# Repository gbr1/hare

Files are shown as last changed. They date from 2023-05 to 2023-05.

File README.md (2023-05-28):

# hare

An open source and open hardware implementation for 4-wheeled mobile robots.

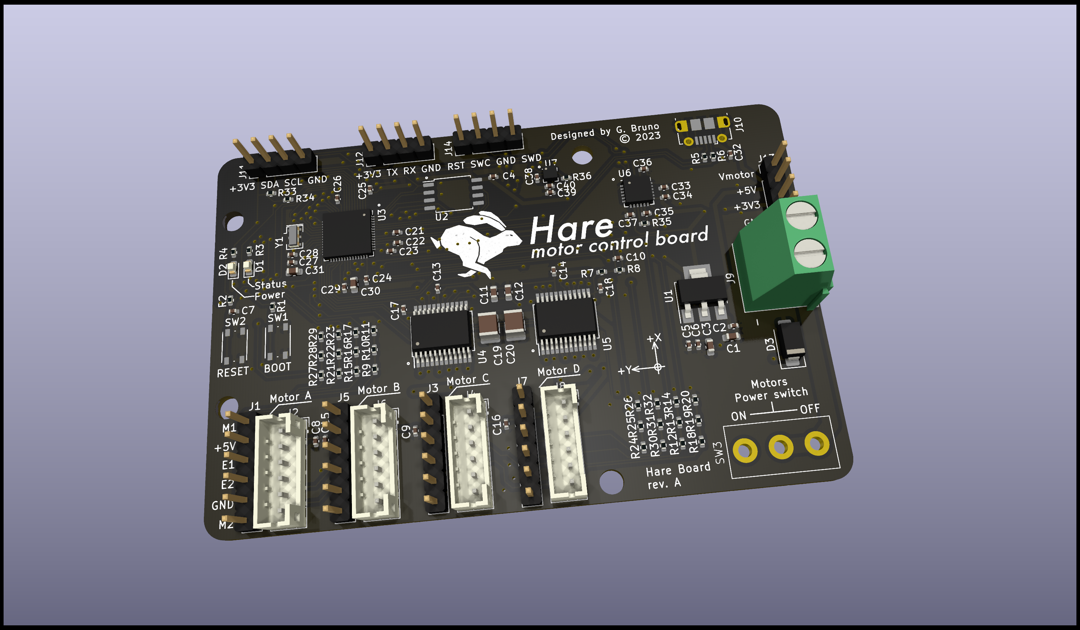
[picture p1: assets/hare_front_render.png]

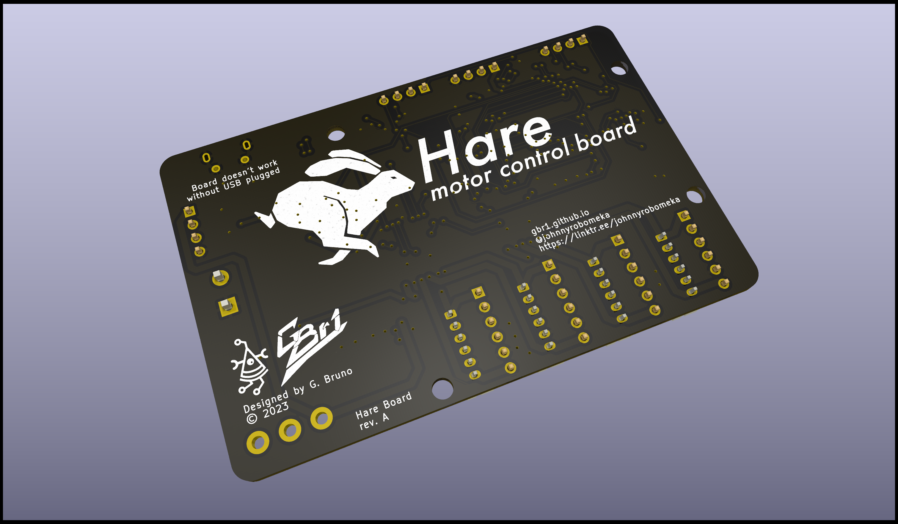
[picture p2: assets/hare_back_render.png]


It is compatible with ROS2 and DC brushed motors with encoder.

## Tech specs

- RP2040 MCU

- dual TB6612FNG motor drivers

- MPU6050 6DoF IMU

- LIS3MDL 3 axis magnetometer

- Power switch only for motors power supply

- 10-15V power input

- external connectors for I2C, debugger and UART

- compatibility with common motors with encoder (e.g. [moebiustech gearmotor](https://it.aliexpress.com/item/4000149449495.html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))

## License

The board is under **CC-4.0-BY-SA-NC** but ***dual licensing is available.***

<br>

For more info contact me.

## Links

- [firmware](https://github.com/gbr1/hare-arduino)

- [website](https://gbr1.github.io)

- [pizzarobotics](https://pizzarobotics.org)

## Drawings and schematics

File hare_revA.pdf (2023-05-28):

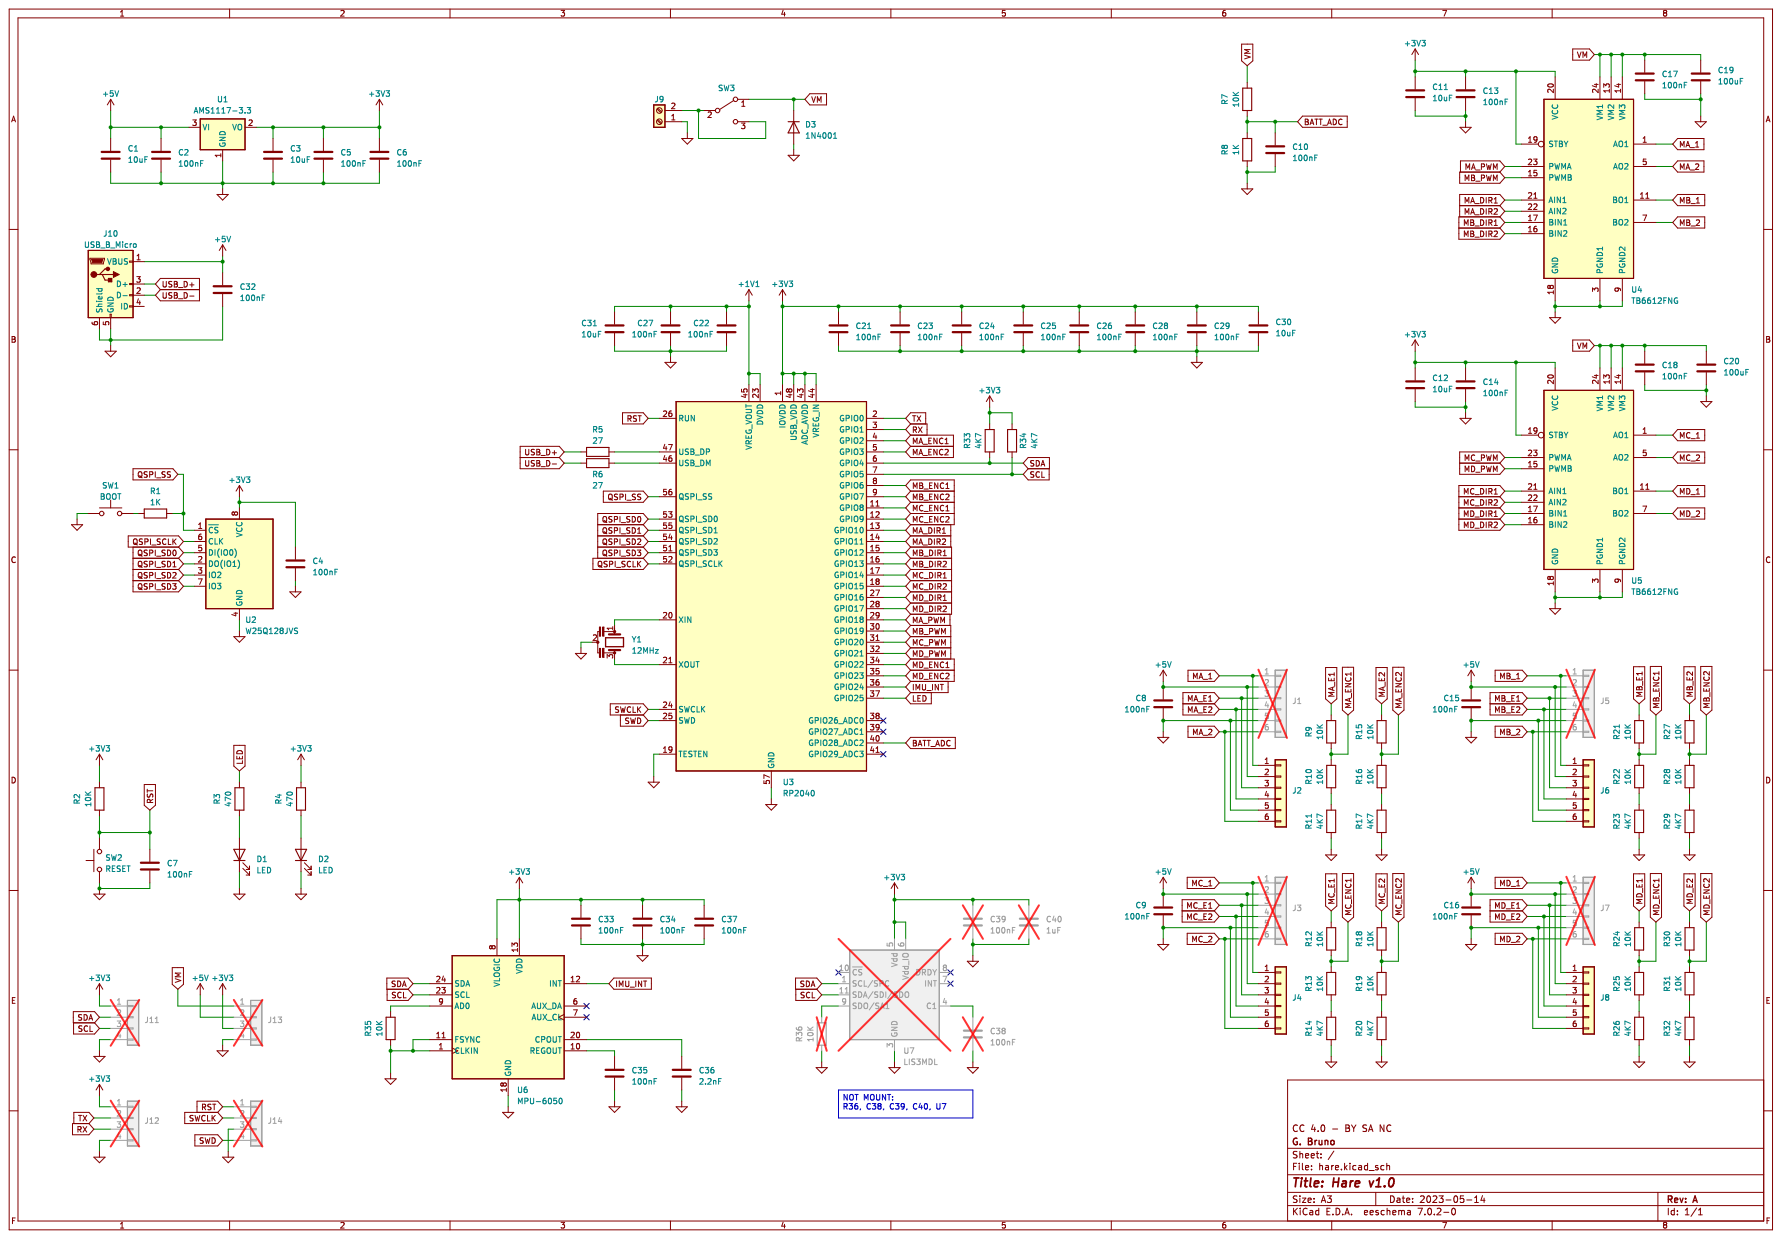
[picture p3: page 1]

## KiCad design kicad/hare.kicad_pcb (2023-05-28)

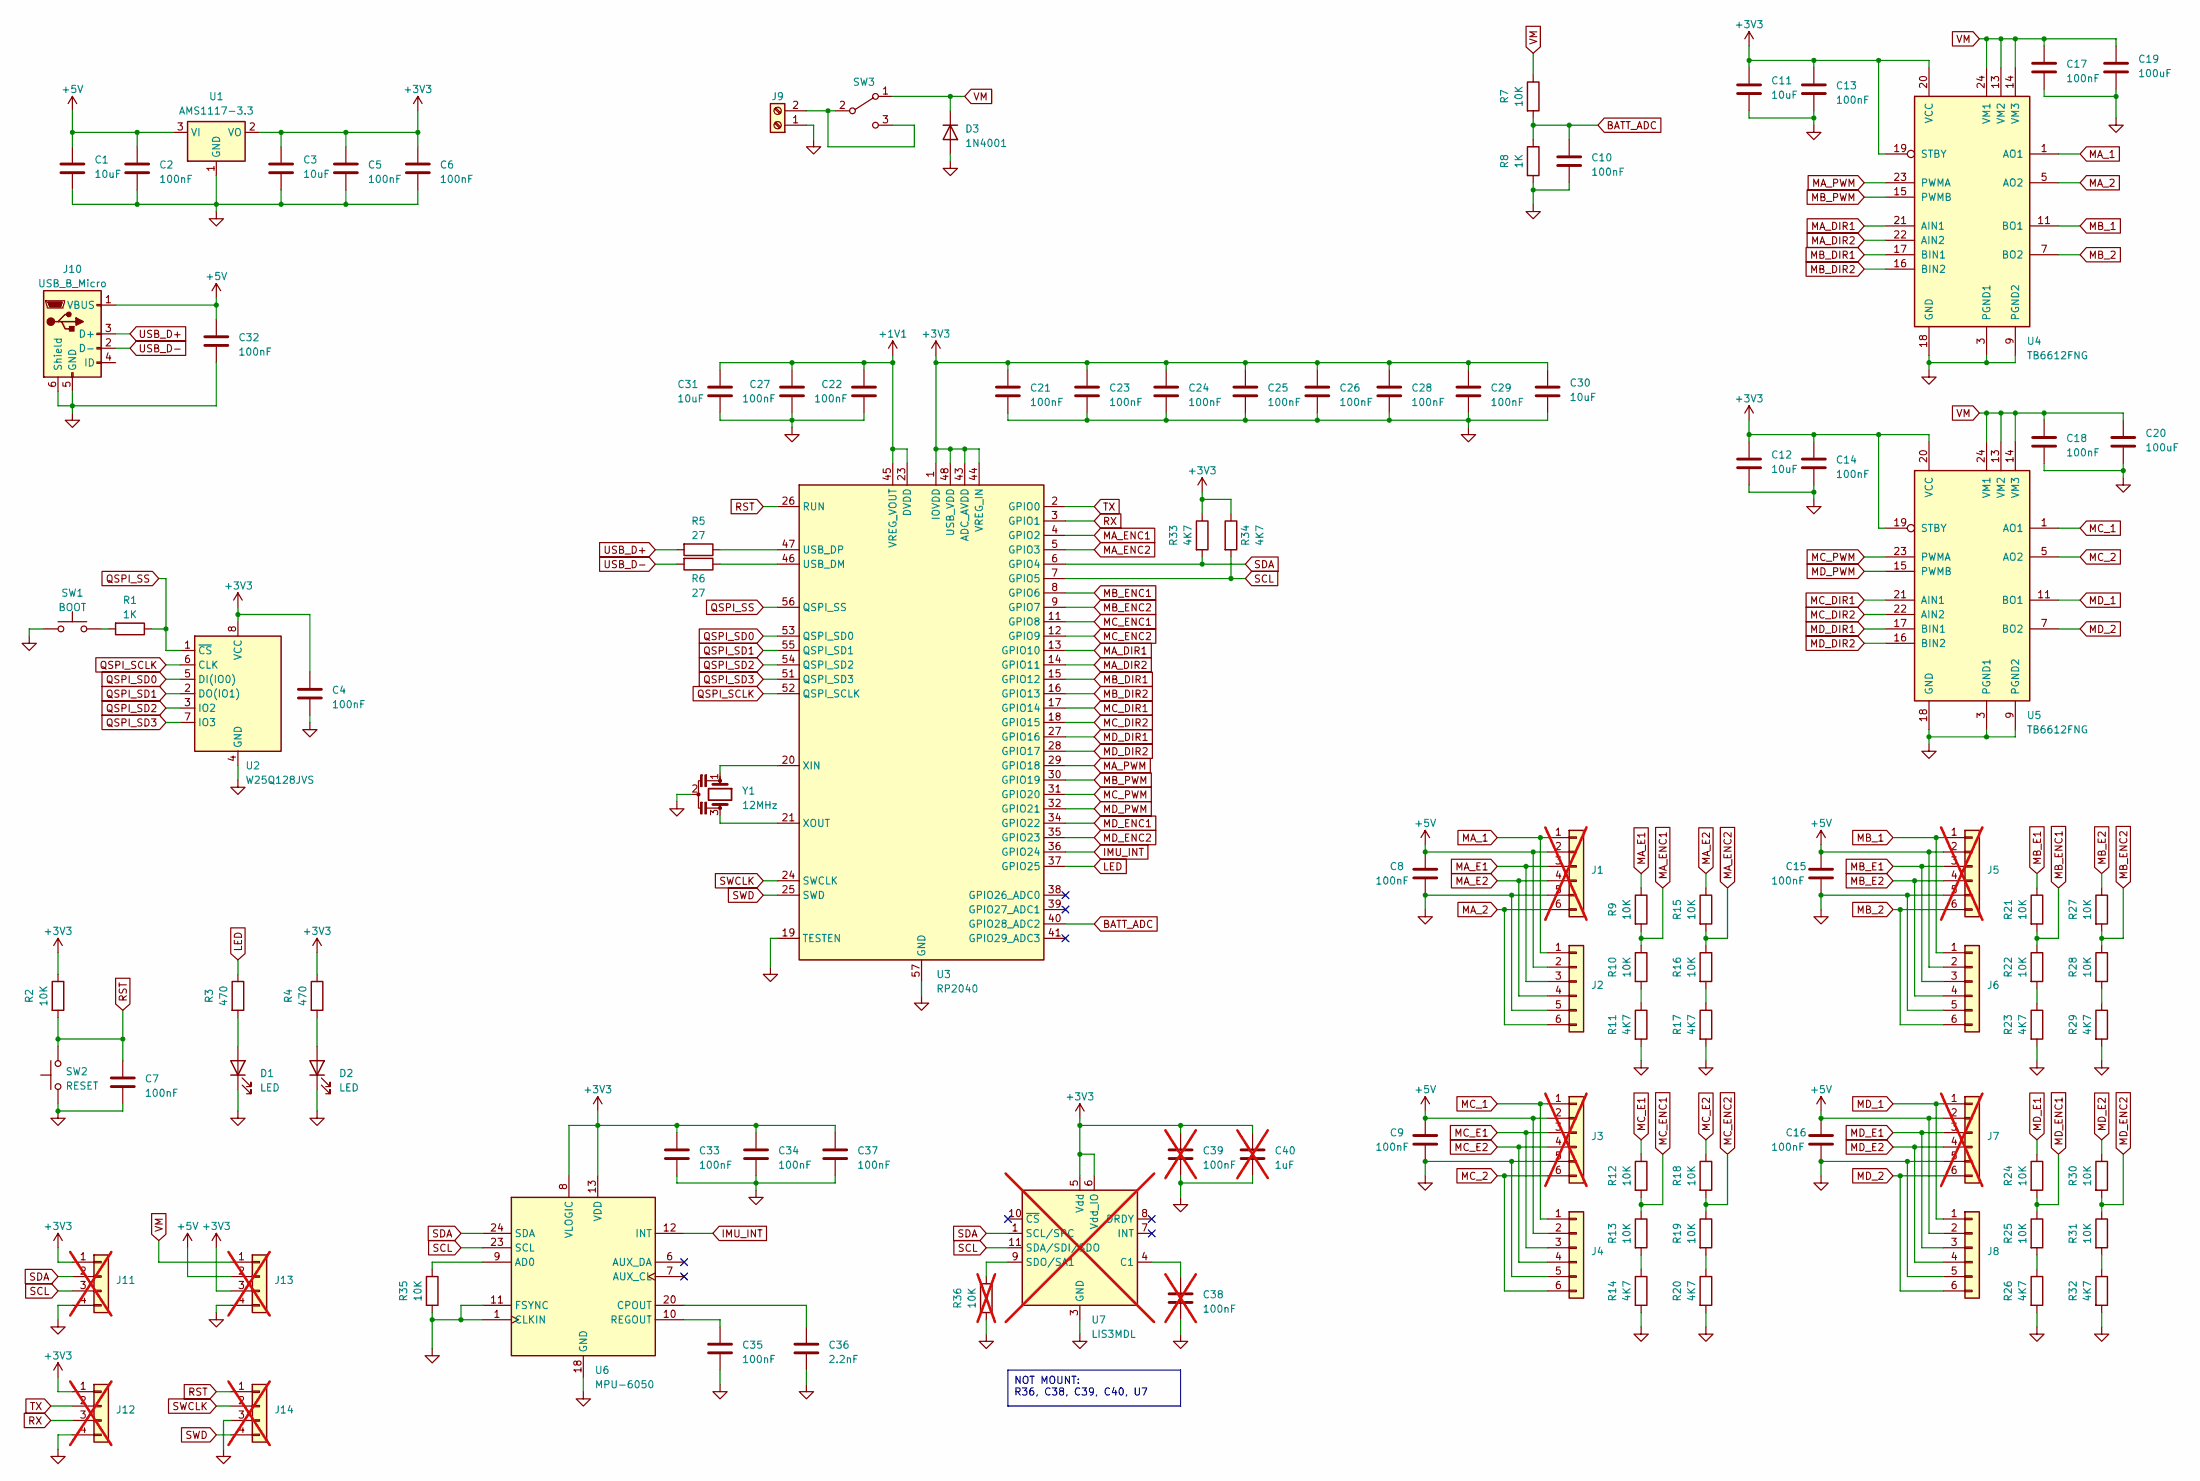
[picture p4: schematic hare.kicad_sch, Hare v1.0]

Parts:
C1, C3, C11, C12, C30, C31: 10uF; C_0603_1608Metric; LCSC Part # C85713
C2, C4, C5, C6, C7, C8, C9, C10, C13, C14, C15, C16, C17, C18, C21, C22, C23, C24, C25, C26, C27, C28, C29, C32, C33, C34, C35, C37: 100nF; C_0402_1005Metric; LCSC Part # C1525
C19, C20: 100uF; C_1210_3225Metric; LCSC Part # C90143
C36: 2.2nF; C_0402_1005Metric; LCSC Part # C106861
C38, C39: 100nF; C_0402_1005Metric; LCSC Part # C1525; not fitted
C40: 1uF; C_0402_1005Metric; LCSC Part # C913556; not fitted
D1: LED; LED_0603_1608Metric; LCSC Part # C72041
D2: LED; LED_0603_1608Metric; LCSC Part # C84263
D3: 1N4001; D_SMA; LCSC Part # C727079
J1, J3, J5, J7: PinHeader_1x06_P2.54mm_Vertical; not fitted
J2, J4, J6, J8: JST_PH_B6B-PH-K_1x06_P2.00mm_Vertical; LCSC Part # C131342
J9: TerminalBlock_Phoenix_MKDS-1,5-2-5.08_1x02_P5.08mm_Horizont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; LCSC Part # C8465
J10: USB_B_Micro; USB_Micro-B_Molex-105017-0001; LCSC Part # C136000
J11, J12, J13, J14: PinHeader_1x04_P2.54mm_Vertical; not fitted
R1, R8: 1K; R_0402_1005Metric; LCSC Part # C3015791
R2, R7, R9, R10, R12, R13, R15, R16, R18, R19, R21, R22, R24, R25, R27, R28, R30, R31, R35: 10K; R_0402_1005Metric; LCSC Part # C3015825
R3, R4: 470; R_0402_1005Metric; LCSC Part # C3015779
R5, R6: 27; R_0402_1005Metric; LCSC Part # C3017455
R11, R14, R17, R20, R23, R26, R29, R32, R33, R34: 4K7; R_0402_1005Metric; LCSC Part # C3015810
R36: 10K; R_0402_1005Metric; LCSC Part # C3015825; not fitted
SW1: BOOT; SW_Push_1P1T_NO_Vertical_Wuerth_434133025816; LCSC Part # C139797
SW2: RESET; SW_Push_1P1T_NO_Vertical_Wuerth_434133025816; LCSC Part # C139797
SW3: XKB-Connectivity-SS-12D10L5; LCSC Part # C319012
U1: AMS1117-3.3; SOT-223-3_TabPin2; LCSC Part # C6186
U2: W25Q128JVS; SOIC-8_5.23x5.23mm_P1.27mm; LCSC Part # C97521
U3: RP2040; QFN-56-1EP_7x7mm_P0.4mm_EP3.2x3.2mm; LCSC Part # C2040
U4, U5: TB6612FNG; SSOP-24_5.3x8.2mm_P0.65mm; LCSC Part # C141517
U6: MPU-6050; InvenSense_QFN-24_4x4mm_P0.5mm; LCSC Part # C24112
U7: LIS3MDL; LGA-12_2x2mm_P0.5mm; LCSC Part # C478483; not fitted
Y1: 12MHz; Resonator_SMD_Murata_CSTxExxV-3Pin_3.0x1.1mm; LCSC Part # C907957

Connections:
+1V1: C22.1, C27.1, C31.1, U3.23 (DVDD), U3.45 (VREG_VOUT), U3.50 (DVDD)
+3V3: C3.1, C4.1, C5.1, C6.1, C11.1, C12.1, C13.1, C14.1, C21.1, C23.1, C24.1, C25.1, C26.1, C28.1, C29.1, C30.1, C33.1, C34.1, C37.1, C39.1, C40.1, J11.1, J12.1, J13.3, R2.1, R4.1, R33.1, R34.1, U1.2 (VO), U2.8 (VCC), U3.1 (IOVDD), U3.10 (IOVDD), U3.22 (IOVDD), U3.33 (IOVDD), U3.42 (IOVDD), U3.43 (ADC_AVDD), U3.44 (VREG_IN), U3.48 (USB_VDD), U3.49 (IOVDD), U4.19 (STBY), U4.20 (VCC), U5.19 (STBY), U5.20 (VCC), U6.8 (VLOGIC), U6.13 (VDD), U7.5 (Vdd), U7.6 (Vdd_IO)
+5V: C1.1, C2.1, C8.1, C9.1, C15.1, C16.1, C32.1, J1.2, J2.2, J3.2, J4.2, J5.2, J6.2, J7.2, J8.2, J10.1 (VBUS), J13.2, U1.3 (VI)
BATT_ADC: C10.1, R7.2, R8.1, U3.40 (GPIO28_ADC2)
GND: C1.2, C2.2, C3.2, C4.2, C5.2, C6.2, C7.2, C8.2, C9.2, C10.2, C11.2, C12.2, C13.2, C14.2, C15.2, C16.2, C17.2, C18.2, C19.2, C20.2, C21.2, C22.2, C23.2, C24.2, C25.2, C26.2, C27.2, C28.2, C29.2, C30.2, C31.2, C32.2, C33.2, C34.2, C35.2, C36.2, C37.2, C38.2, C39.2, C40.2, D1.1 (K), D2.1 (K), D3.2 (A), J1.5, J2.5, J3.5, J4.5, J5.5, J6.5, J7.5, J8.5, J9.1, J10.5 (GND), J10.6 (Shield), J11.4, J12.4, J13.4, J14.3, R8.2, R11.2, R14.2, R17.2, R20.2, R23.2, R26.2, R29.2, R32.2, R35.2, R36.2, SW1.1, SW2.1, U1.1 (GND), U2.4 (GND), U3.19 (TESTEN), U3.57 (GND), U4.3 (PGND1), U4.4 (PGND1), U4.9 (PGND2), U4.10 (PGND2), U4.18 (GND), U5.3 (PGND1), U5.4 (PGND1), U5.9 (PGND2), U5.10 (PGND2), U5.18 (GND), U6.1 (CLKIN), U6.11 (FSYNC), U6.18 (GND), U7.2 (GND), U7.3 (GND), U7.12 (GND), Y1.2
IMU_INT: U3.36 (GPIO24), U6.12 (INT)
LED: R3.1, U3.37 (GPIO25)
MA_1: J1.1, J2.1, U4.1 (AO1), U4.2 (AO1)
MA_2: J1.6, J2.6, U4.5 (AO2), U4.6 (AO2)
MA_DIR1: U3.13 (GPIO10), U4.21 (AIN1)
MA_DIR2: U3.14 (GPIO11), U4.22 (AIN2)
MA_E1: J1.3, J2.3, R9.1
MA_E2: J1.4, J2.4, R15.1
MA_ENC1: R9.2, R10.1, U3.4 (GPIO2)
MA_ENC2: R15.2, R16.1, U3.5 (GPIO3)
MA_PWM: U3.29 (GPIO18), U4.23 (PWMA)
MB_1: J5.1, J6.1, U4.11 (BO1), U4.12 (BO1)
MB_2: J5.6, J6.6, U4.7 (BO2), U4.8 (BO2)
MB_DIR1: U3.15 (GPIO12), U4.17 (BIN1)
MB_DIR2: U3.16 (GPIO13), U4.16 (BIN2)
MB_E1: J5.3, J6.3, R21.1
MB_E2: J5.4, J6.4, R27.1
MB_ENC1: R21.2, R22.1, U3.8 (GPIO6)
MB_ENC2: R27.2, R28.1, U3.9 (GPIO7)
MB_PWM: U3.30 (GPIO19), U4.15 (PWMB)
MC_1: J3.1, J4.1, U5.1 (AO1), U5.2 (AO1)
MC_2: J3.6, J4.6, U5.5 (AO2), U5.6 (AO2)
MC_DIR1: U3.17 (GPIO14), U5.21 (AIN1)
MC_DIR2: U3.18 (GPIO15), U5.22 (AIN2)
MC_E1: J3.3, J4.3, R12.1
MC_E2: J3.4, J4.4, R18.1
MC_ENC1: R12.2, R13.1, U3.11 (GPIO8)
MC_ENC2: R18.2, R19.1, U3.12 (GPIO9)
MC_PWM: U3.31 (GPIO20), U5.23 (PWMA)
MD_1: J7.1, J8.1, U5.11 (BO1), U5.12 (BO1)
MD_2: J7.6, J8.6, U5.7 (BO2), U5.8 (BO2)
MD_DIR1: U3.27 (GPIO16), U5.17 (BIN1)
MD_DIR2: U3.28 (GPIO17), U5.16 (BIN2)
MD_E1: J7.3, J8.3, R24.1
MD_E2: J7.4, J8.4, R30.1
MD_ENC1: R24.2, R25.1, U3.34 (GPIO22)
MD_ENC2: R30.2, R31.1, U3.35 (GPIO23)
MD_PWM: U3.32 (GPIO21), U5.15 (PWMB)
unnamed: D1.2 (A), R3.2
unnamed: D2.2 (A), R4.2
unnamed: J9.2, SW3.2 (B), SW3.3 (C)
unnamed: R1.2, SW1.2
unnamed: R10.2, R11.1
unnamed: R13.2, R14.1
unnamed: R16.2, R17.1
unnamed: R19.2, R20.1
unnamed: R22.2, R23.1
unnamed: R25.2, R26.1
unnamed: R28.2, R29.1
unnamed: R31.2, R32.1
unnamed: R6.1, U3.46 (USB_DM)
unnamed: R5.1, U3.47 (USB_DP)
unnamed: U3.20 (XIN), Y1.1
unnamed: U3.21 (XOUT), Y1.3
unnamed: R35.1, U6.9 (AD0)
unnamed: C36.1, U6.20 (CPOUT)
unnamed: C35.1, U6.10 (REGOUT)
unnamed: C38.1, U7.4 (C1)
unnamed: R36.1, U7.9 (SDO/SA1)
QSPI_SCLK: U2.6 (CLK), U3.52 (QSPI_SCLK)
QSPI_SD0: U2.5 (DI(IO0)), U3.53 (QSPI_SD0)
QSPI_SD1: U2.2 (DO(IO1)), U3.55 (QSPI_SD1)
QSPI_SD2: U2.3 (IO2), U3.54 (QSPI_SD2)
QSPI_SD3: U2.7 (IO3), U3.51 (QSPI_SD3)
QSPI_SS: R1.1, U2.1 (~CS), U3.56 (QSPI_SS)
RST: C7.1, J14.1, R2.2, SW2.2, U3.26 (RUN)
RX: J12.3, U3.3 (GPIO1)
SCL: J11.3, R34.2, U3.7 (GPIO5), U6.23 (SCL), U7.11 (SDA/SDI/SDO)
SDA: J11.2, R33.2, U3.6 (GPIO4), U6.24 (SDA), U7.1 (SCL/SPC)
SWCLK: J14.2, U3.24 (SWCLK)
SWD: J14.4, U3.25 (SWD)
TX: J12.2, U3.2 (GPIO0)
USB_D+: J10.3 (D+), R5.2
USB_D-: J10.2 (D-), R6.2
VM: C17.1, C18.1, C19.1, C20.1, D3.1 (K), J13.1, R7.1, SW3.1 (A), U4.13 (VM2), U4.14 (VM3), U4.24 (VM1), U5.13 (VM2), U5.14 (VM3), U5.24 (VM1)

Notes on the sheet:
NOT MOUNT: R36, C38, C39, C40, U7

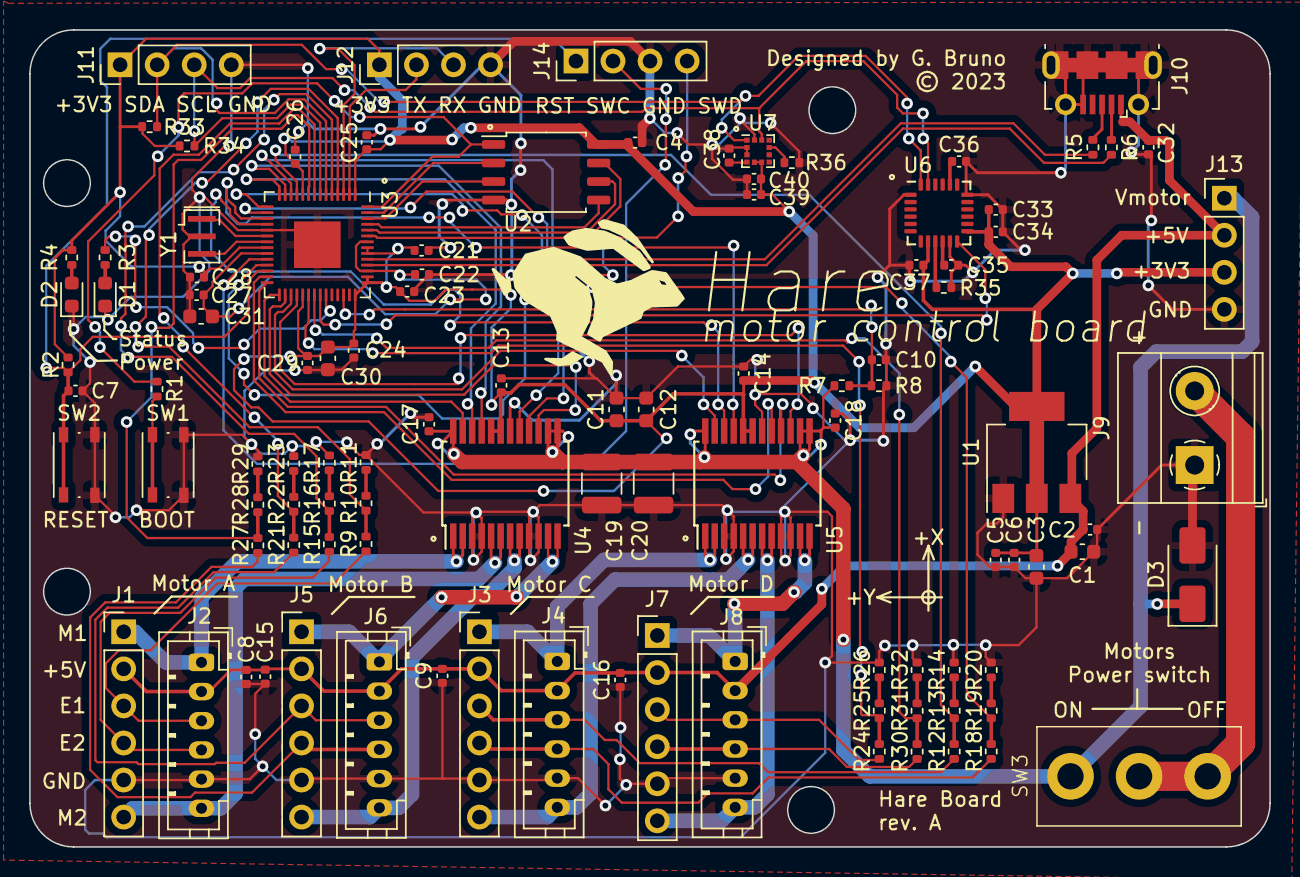
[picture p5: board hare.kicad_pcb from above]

Board: 2 copper layers, 85.0 x 56.0 mm, 104 parts (0 on the bottom side), 80 nets.

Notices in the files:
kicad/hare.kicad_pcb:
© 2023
